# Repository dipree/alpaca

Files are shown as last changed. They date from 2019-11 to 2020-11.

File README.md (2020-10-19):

# Alpaca 🦙
The Alpaca is a lightweight, 5", cinematic, all-round quadcopter frame with long-range capabilities designed for 20x20mm mounting pattern components. The squished x-design with a 225mm motor to motor distance gives space for clean air and stability. The front frame section is on a level with the front motors which allows to get camera shots without propellers in view.

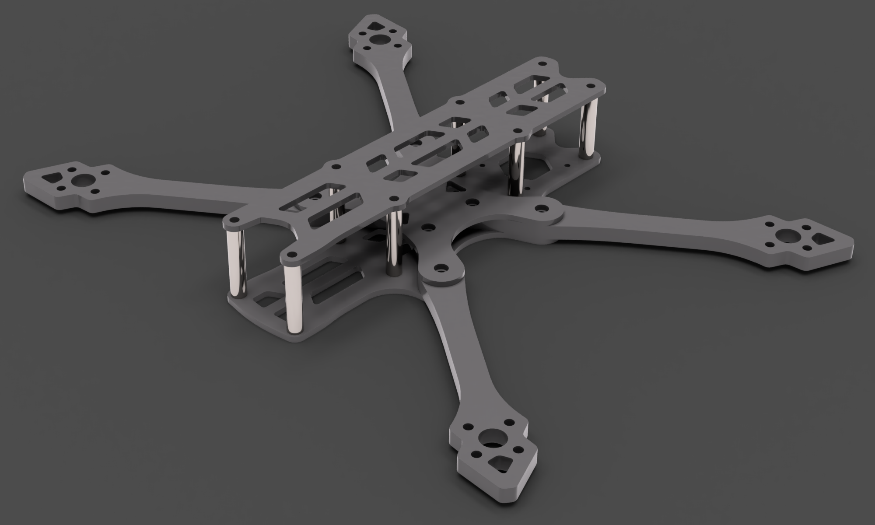
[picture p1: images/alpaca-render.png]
Alpaca frame render image


## Specifications
* Wheelbase: 225mm (fits 5.1" propellers)
* Standoff height: 25mm
* Motor mount: 16x16mm
* Stack mount options:
  * Center 20x20mm M3
  * Rear 20x20 M2
* Camera width: max. 21mm (Mini size)
* Carbon weight: 73.7g

### Carbon fiber plates
All carbon fiber parts are at [alpaca/frame](https://github.com/dipree/alpaca/tree/master/frame), ready to cut.
* Top plate: 2mm
* Center plate: 2mm
* Bottom plate: 2mm
* Arm thickness: 5mm

**Blueprint**

Alpaca frame render image

### Accessoires
Ready to print `.stl` files for different applications are at [alpaca/accessories/](https://github.com/dipree/alpaca/tree/master/accessories). Best results can be achieved with SainSmart TPU.

## Required Hardware
* 12 x M3/6mm button head screw
* 4 x M3/6mm countersunk screw
* 16 x M3/8mm button head screw
* 4 x M3/12mm button head screw
* 4 x M3/14mm button head screw
* 8 x M3/25mm standoffs
* 8 x M3 press nuts to fit 4.5mm holes

## Recommended Build
The four rear holes on the top plate should be prepared for countersunk screws. This way the battery won't be damaged by the screw heads. With all steel screws and aluminum standoffs the total frame weight is around ~93.4g. The center stack should be soft-mounted, for example rubber o-rings underneath the electronic speed controller and rubber standoffs to mount the flight controller on top. There's 3D printable adapters for the FPV camera. Weight is key of this frame, take caution when adding extraneous parts.

## Where to get?
Download the [latest release](https://github.com/derpixeldan/alpaca/releases/) and send the `.dxf` frame files alongside with the above [instructions](#carbon-fiber-plates) to a carbon fiber cutting service, for example [cnc madness](https://cncmadness.com/).

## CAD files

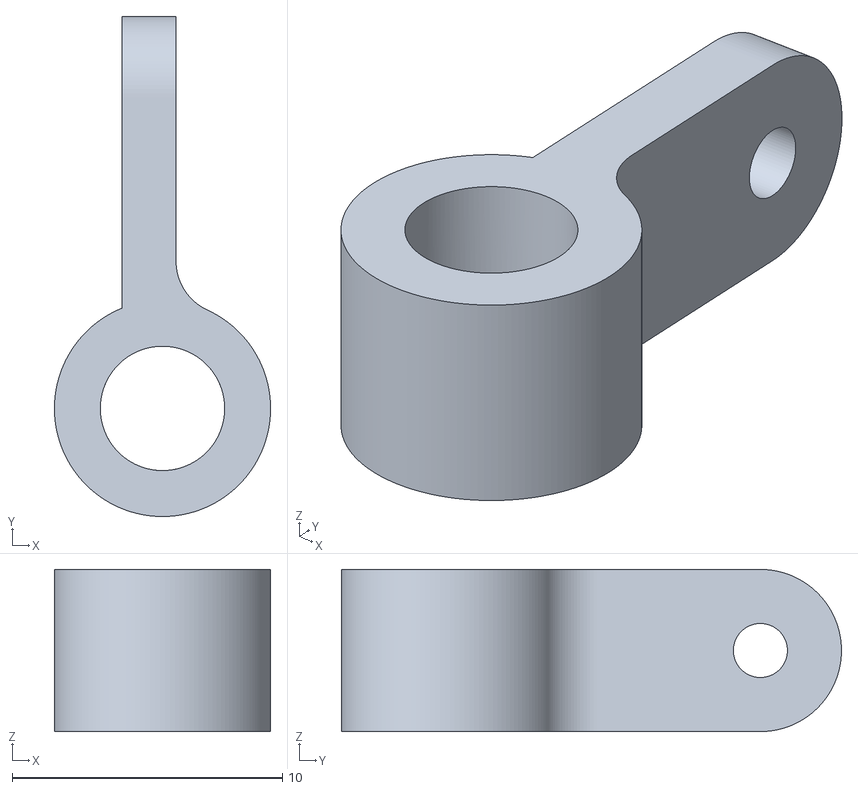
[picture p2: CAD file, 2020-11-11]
accessories/camera_mount_mini.stl
8.00 x 18.5 x 6.00

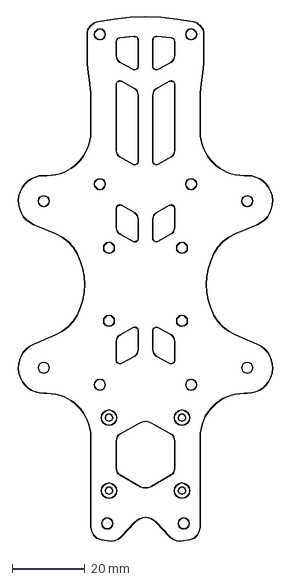
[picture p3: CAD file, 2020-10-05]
frame/bottom_plate.dxf
70.8 x 144.1 mm

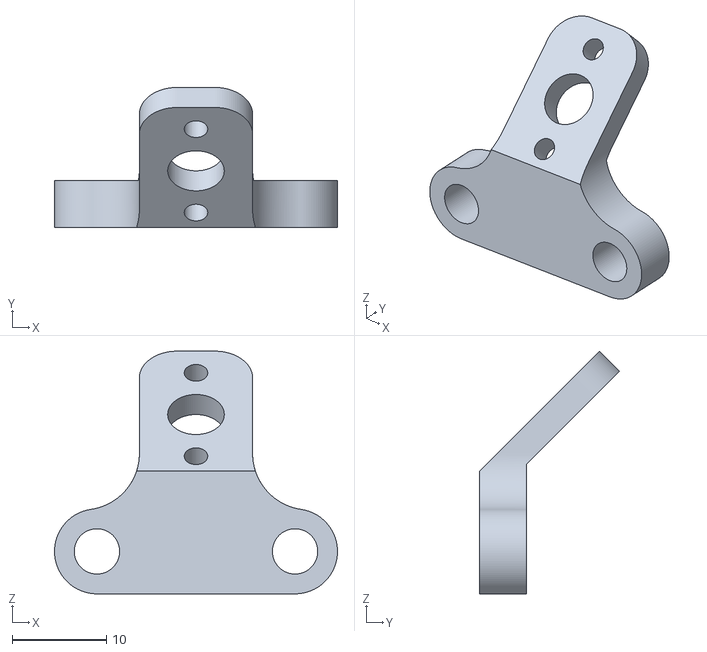
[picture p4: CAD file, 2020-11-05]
accessories/pigtail_mount_extended.stl
30.0 x 14.8 x 25.7

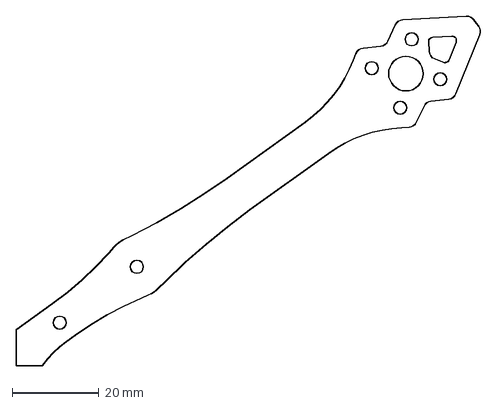
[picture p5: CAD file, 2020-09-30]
frame/arm.dxf
107.3 x 80.8 mm

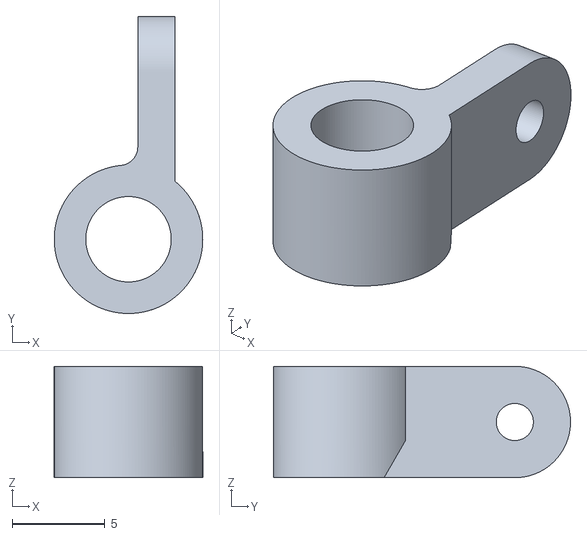
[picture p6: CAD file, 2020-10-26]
accessories/camera_mount_dji_right.stl
8.00 x 16.0 x 6.00

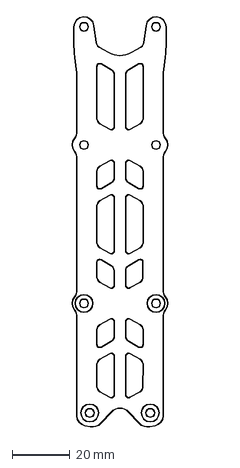
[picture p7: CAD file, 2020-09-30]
frame/top_plate.dxf
33.5 x 142.7 mm

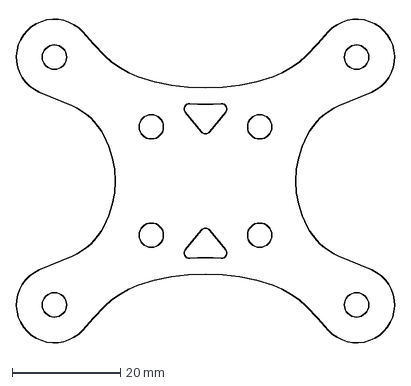
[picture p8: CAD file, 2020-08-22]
frame/center_plate.dxf
69.9 x 60.8 mm

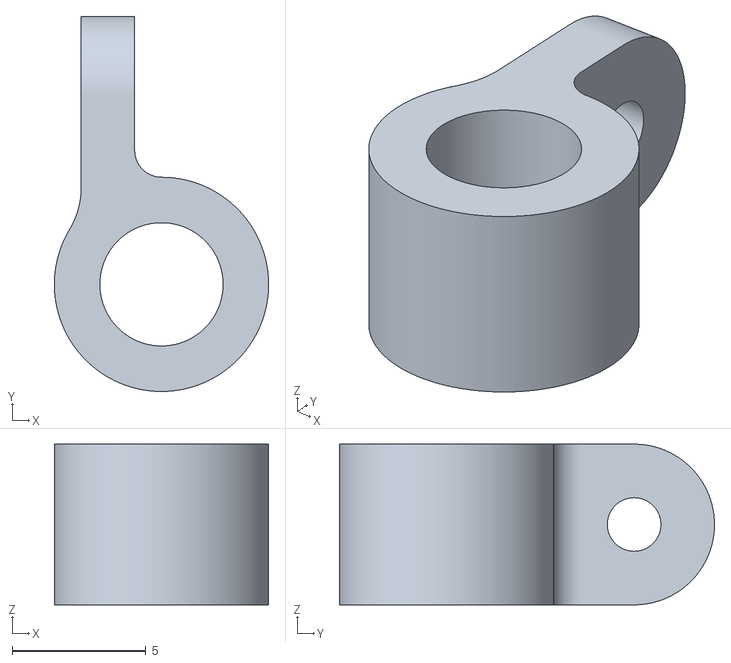
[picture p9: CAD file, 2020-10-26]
accessories/camera_mount_micro.stl
8.00 x 14.0 x 6.00

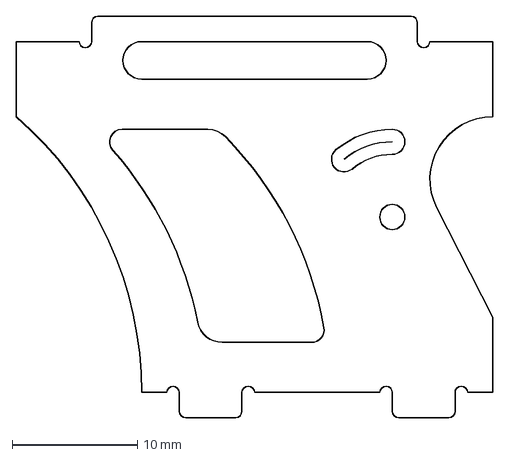
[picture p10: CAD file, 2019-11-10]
frame/cam_plate.dxf
38.0 x 32.0 mm

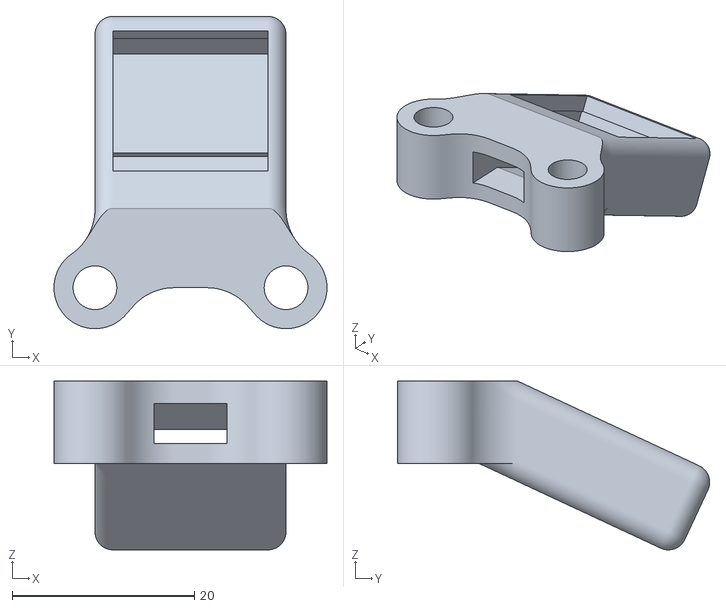
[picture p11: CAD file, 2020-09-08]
accessories/gps_mount.stl
30.0 x 34.3 x 18.5

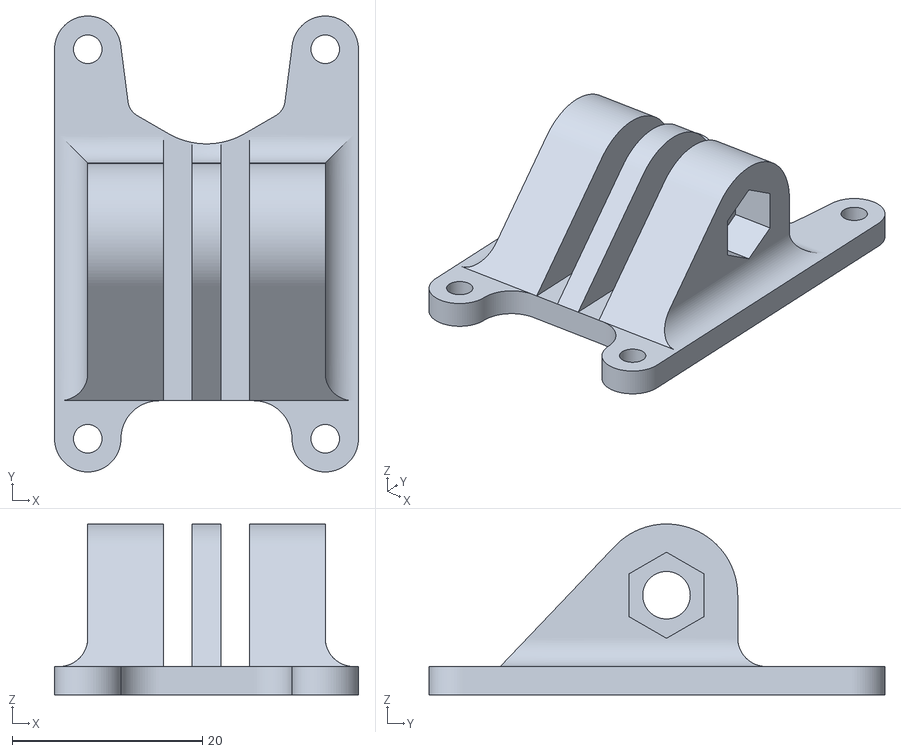
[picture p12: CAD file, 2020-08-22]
accessories/gopro_mount_adapter.stl
32.0 x 48.0 x 18.0

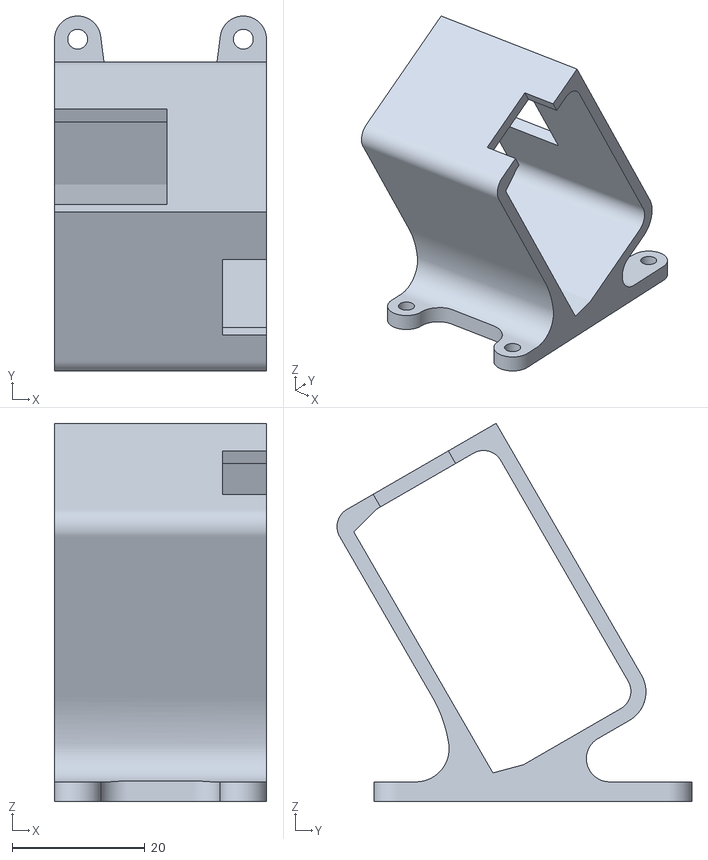
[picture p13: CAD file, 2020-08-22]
accessories/gopro_mount_hero6and7.stl
32.0 x 53.6 x 57.1

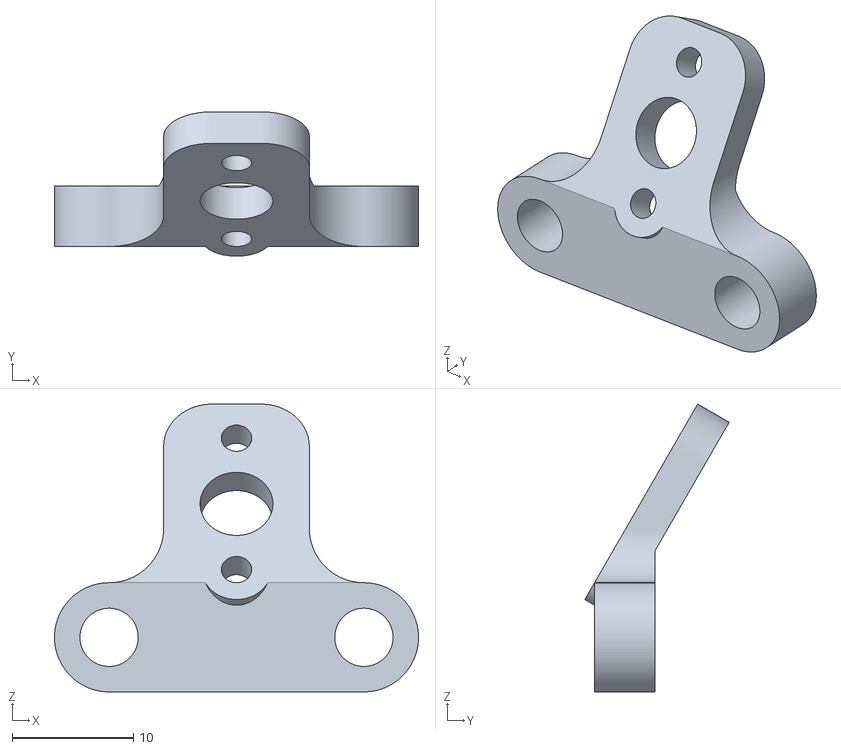
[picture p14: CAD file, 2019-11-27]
accessories/pigtail_mount_unify.stl
30.0 x 11.9 x 23.7

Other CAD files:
accessories/camera_mount_dji_left.stl

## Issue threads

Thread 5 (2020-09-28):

Bottom plate has surface cracks

dipree, 2020-09-28:
When crashing on the rear or front the bending might cause cracks in the first layer of carbon around the second and third row of standoffs. The cutouts seem to weaken the structure around the standoffs.

**Potential solution:** Remove cutouts around standoffs so the force can be swallowed better.

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

Closed 2020-09-30.

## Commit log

2019-08-17 Add frame files
    [Arm.dxf, Bottom_Plate.dxf, Cam_Plate.dxf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]
2019-08-17 Update readme with “where to get” section
2019-08-19 Add camera mount for micro eagle
    [Cam_Mount-Micro_Eagle.stl]
2019-08-20 Fix micro eagle cam mount
    [Cam_Mount-Micro_Eagle.stl]
2019-08-21 Add carbon weight of latest version
    Remove 5mm screws as they’re not needed anymore
2019-10-05 Add pigtail mount
    [Pigtail_Mount.stl]
2019-10-05 Update all frame files
    [Arm.dxf, Bottom_Plate.dxf, Cam_Plate.dxf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]
2019-10-05 Remove Micro Eagle cam mount
    Won’t fit anymore.
    [Cam_Mount-Micro_Eagle.stl]
2019-11-13 Slightly strengthen arms and connection
    [Arm.dxf, Bottom_Plate.dxf, Center_Plate.dxf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]
2019-11-22 Rename files Uppercase -> lowercase
    [arm.dxf, bottom_plate.dxf, cam_plate.dxf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]
2019-11-22 Add foxeer compatible cam_plate
    [cam_plate_foxeer.dxf]
2019-11-22 Update and rename runcam cam plate
    [cam_plate_runcam.dxf]
2019-11-22 Update to interlocking arms
    [arm.dxf]
2019-11-25 Add new pigtail mount
    Delete old one.
    [pigtail_mount.stl, pigtail_mount_unify.stl]
2019-11-27 Update pigtail mount for tighter fit
    [pigtail_mount_unify.stl]
2019-12-15 Fix cam plates
    Vertical position was too low so the camera couldn’t be tilted more than 30°.
    [cam_plate_foxeer.dxf, cam_plate_runcam.dxf]
2020-02-13 Update frame files to fit new arm size
    [arm.dxf, bottom_plate.dxf, center_plate.dxf]
2020-02-13 Adjust top plate cut outs
    [top_plate.dxf]
2020-03-04 Update wireframe rendering
2020-03-07 Add new 230mm hero render
2020-03-16 Remove wireframes from Readme
2020-05-17 Add hero 6/7 mount
    [camera_mount_hero6and7.stl]
2020-06-03 Shorten arms to 225mm
    [arm.dxf]
2020-06-03 Shorten front and rear section
    Front by 4mm, rear by 2mm
    [bottom_plate.dxf, cam_plate_runcam.dxf, top_plate.dxf]
2020-06-03 Update center_plate to match bottom_plate
    [center_plate.dxf]
2020-07-03 Update cam plate to match new front length
    [cam_plate_foxeer.dxf, cam_plate_runcam.dxf]
2020-07-03 Add cam plate for micro cameras
    [cam_plate_micro.dxf]
2020-07-15 Add countersunk indicators to top plate
    [top_plate.dxf]
2020-07-30 Slightly tighter fit
    [camera_mount_hero6and7.stl]
2020-07-30 Add camera mount adapter
    [camera_mount_adapter_hero.stl]
2020-07-30 Tweak countersunk cutouts
    [top_plate.dxf]
2020-08-02 Beefier version of the adapter mount
    [camera_mount_adapter_hero.stl]
2020-08-26 Change cutouts slightly
    [arm.dxf, bottom_plate.dxf, top_plate.dxf]
2020-09-08 Add gps mount accessory
    [gps_mount.stl]
2020-09-30 Update cutouts and add 20x20 mount to rear
    [arm.dxf, bottom_plate.dxf, top_plate.dxf]
2020-09-30 Remove cam plates
    [cam_plate_foxeer.dxf, cam_plate_micro.dxf, cam_plate_runcam.dxf]
2020-10-04 Fix arc glitch
    [bottom_plate.dxf]
2020-10-05 Add countersunk indicator for M2
    [bottom_plate.dxf]
2020-10-26 Add micro cam mount accessory
    [camera_mount_micro.stl]
2020-10-26 Add dji cam mount accessory
    [camera_mount_dji_left.stl, camera_mount_dji_right.stl]
2020-10-26 Rename gopro mounts
    [gopro_mount_adapter.stl, gopro_mount_hero6and7.stl]
2020-11-05 Add pigtail extended accessory
    [pigtail_mount_extended.stl]
2020-11-11 Add mini camera mount accessory
    [camera_mount_mini.stl]
